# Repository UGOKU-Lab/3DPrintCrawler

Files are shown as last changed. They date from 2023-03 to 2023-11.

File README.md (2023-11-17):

# 3DPrintCrawlerについて
タミヤのラダーチェーンとギアボックス、3Dプリントパーツのみで製作したクローラユニットです。  
使用するネジ類もタミヤのセットの付属品のみで完結します。  
ラダーチェーンに履板をパッチっとはめる方式なので履板形状を自由に設計できます。

本リポジトリはみなさんにより早くデータを提供するため、README含め不完全な状態で公開する、β版的な位置づけである点をご了承ください。
ご意見や改善案のある方は、Twitter、Issues、プルリクなどで問い合わせ及び提案お願いします。
次期Versionの開発に生かします。

 

# 製作に必要なタミヤの部品
1ユニット製作するのに、それぞれ1セットずつ必要になります。

- 楽しい工作シリーズ（パーツ）No.142 ラダーチェーン＆スプロケットセット  
https://www.tamiya.com/japan/products/70142/index.html

- テクニクラフトシリーズ No.7　4速パワーギヤボックスHE  
https://www.tamiya.com/japan/products/72007/index.html

# データの説明
- フォルダ「stl」：すぐにプリントしたい方向けに各パーツをstlで置いてあります。
- フォルダ「step」：組み立ての確認用、データ編集用です。左右接続したアセンブリのデータと履板のデータをstepで置いてあります。

## データ留意事項
- 履板をプリントする際はアセンブリファイル内のものではなく、個別のデータをご使用ください。プリント用に調整してあります。きつすぎたり、ゆるすぎたりする場合はstepから編集してください。
- アセンブリファイルに含まれる基板はMultiBoardMiniという作者が開発している汎用基板です。こちらについてはデータ公開準備中です。

# 3Dプリント
プリントには250x250サイズ程度の3Dプリンタが必要になります。より普及している220x220サイズのプリンタではプリントできないのでご注意ください。（後日220x220サイズのプリンタでもプリント可能な全長短縮版もアップ予定ですのでもう少々お待ちください。）
すべての部品において充填率は15%ほどで問題ないと思います。
## main-flame
250x250サイズのプリンタでも収めるためには斜めに配置する必要があります。
手前の工具穴、左右接続パーツ挿入部、長穴にはサポートが不要なためサポートブロッカーを配置します。
左右接続パーツ挿入部は条件によりフィラメントが垂れ下がることがありますが、その場合はやすり等で除去してください。おそらくサポート材を外すより楽です。



## track-shoe
サポート材は不要ですが、接地面積が小さいため外れやすいです。外れる場合はBrimを使いましょう。外れるリスクをとるか、Brimを除去する手間をとるかといったかんじです。



## その他パーツ
その他のパーツは積層方向が正しければ特段留意点はありません。

# 組み立て
## 使用工具
- ＋ドライバーNo.2・2本（1本は細軸が望ましい）
- ナットドライバ 5.5
- ニッパー

## 組み立て参考図
- スプロケットとクランクプレートの固定：3×8mmタッピングビス（ラダーチェーン付属）　　
- ギアボックス固定：3×10mmタッピングビス（ギヤボックス付属）
- アイドラシャフト固定：3×12mmタッピングビス（ラダーチェーン付属）















# ライセンス
<br />この 作品 は <a rel="license" href="http://creativecommons.org/licenses/by-sa/4.0/deed.ja">クリエイティブ・コモンズ 表示 4.0 国際 ライセンス</a>の下に提供されています。

本データおよび本データにより製作したクローラーは良識の範囲で自由に非営利、営利問わず使用できます。また、改変、再配布も可能です。
ただし、再配布の際には「3DPrintCrawler」と本リポジトリのリンクを掲載してください。  
また、本データにより製作したクローラーを公の場で使用、SNS等で紹介する場合はなるべく「#3DPrintCrawler」と本リポジトリのリンクを掲載してください。  
また、本データにより生じた損害等の一切の責任を負いかねますので、ご了承ください。

# 今後の展望
今回はInventor（学生ライセンス）でデータを作成[^1]しましたが、次期バージョンはFreeCADなどフリーかつオープンソースの3DCADでデータを作成し、だれでもネイティブで編集できるようにしようと考えています。
また、将来的には寸法を入力するとそのサイズの3Dプリントクローラの3Dモデルが自動生成されるツールにまで発展させたいと考えています。
[^1]:データは学生時代に製作したものです。
# 最後に
本作品は作者の元インターン先でもある**株式会社CuboRex**のクローラユニット「**CuGo**」シリーズにもインスピレーションを受けています。  
また、株式会社タミヤの製品があってこそ実現できました。  
さらに、3Dプリント履板をタミヤのラダーチェーンにはめるというアイデアは研究室にあった機体より得たものです。  
この場をお借りして株式会社CuboRex、株式会社タミヤ、そして先述の機体を製作した研究室の先輩に敬意を表します。

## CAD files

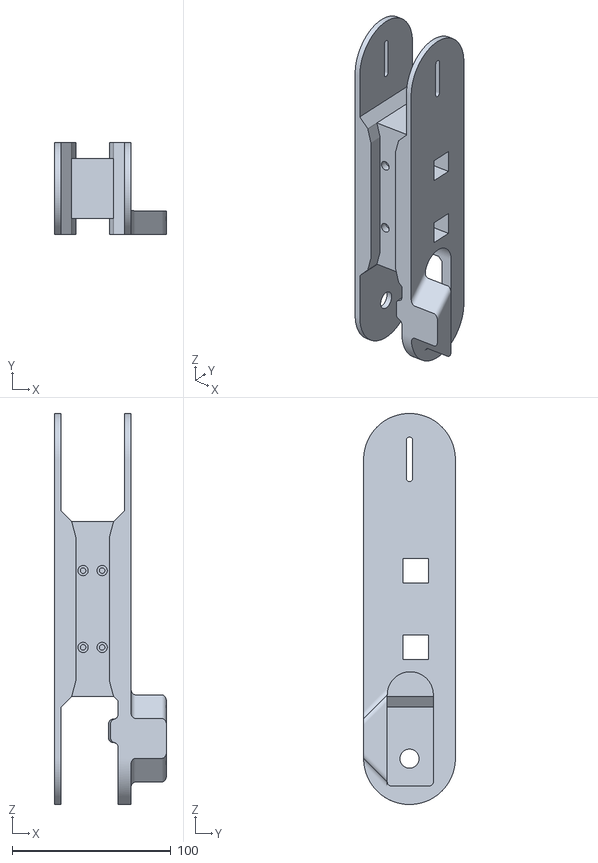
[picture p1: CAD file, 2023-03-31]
stl/main-flame_R.stl
70.5 x 57.7 x 246.0

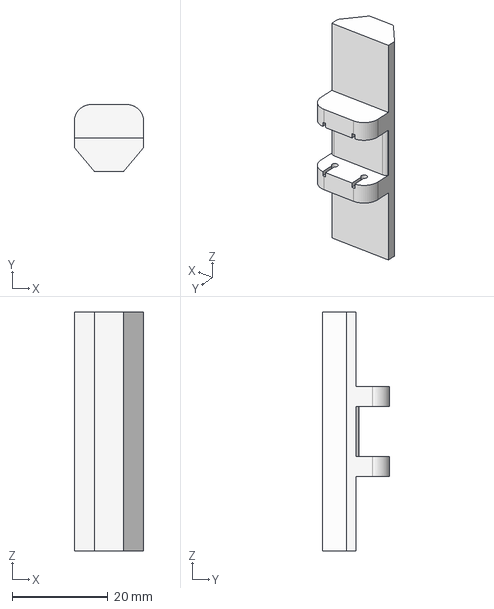
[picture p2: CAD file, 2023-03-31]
step/track-shoe_for_0.5mm-nozzle.step
14.5 x 14.0 x 50.0 mm

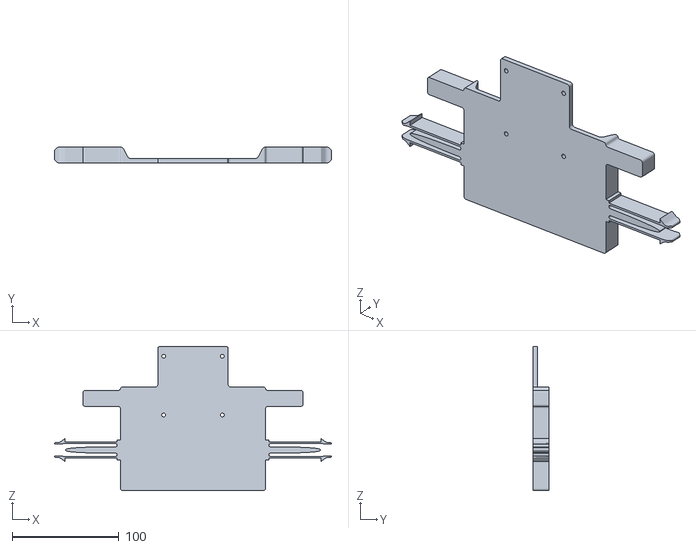
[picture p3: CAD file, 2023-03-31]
stl/center-flame.stl
259.4 x 15.0 x 135.0

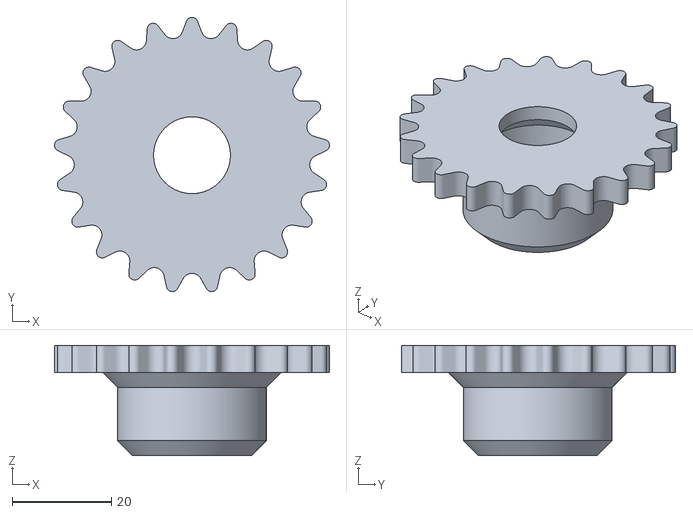
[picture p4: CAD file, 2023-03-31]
stl/Idler.stl
55.5 x 55.4 x 22.2

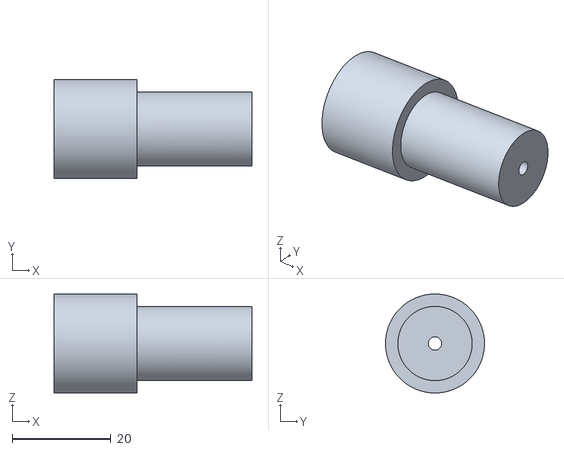
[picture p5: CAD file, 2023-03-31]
stl/idler_shaft.stl
40.0 x 20.0 x 20.0

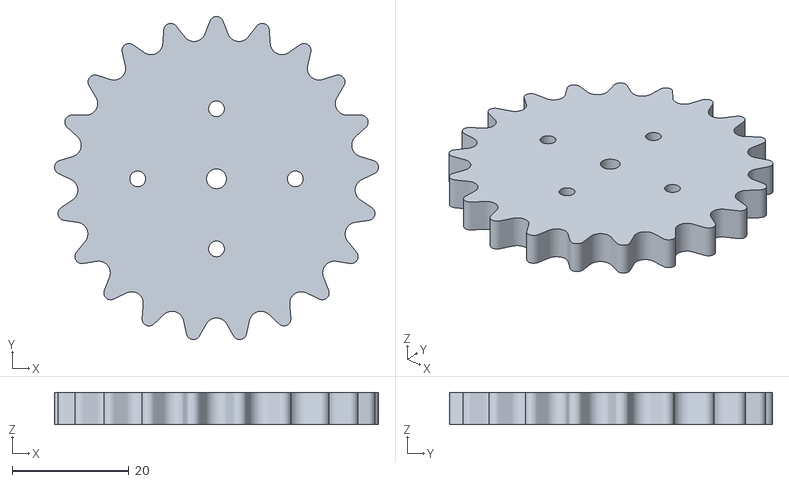
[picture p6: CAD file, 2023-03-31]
stl/sproket.stl
55.5 x 55.4 x 5.50

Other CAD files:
stl/main-flame_L.stl
step/track-shoe_for_0.4mm-nozzle.step
stl/track-shoe_0.5mm_nozzle.stl
stl/track-shoe_0.4mm_nozzle.stl

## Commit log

2023-03-31 add stl
    [Idler.stl, idler_shaft.stl, main-flame_L.stl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]
2023-03-31 add center-flame stl
    [center-flame.stl]
2023-03-31 add step
    [track-shoe_for_0.4mm-nozzle.step, track-shoe_for_0.5mm-nozzle.step]
2023-09-23 Update README.md
    MultiBoardMiniのデータの公開について諸事情により準備中に変更

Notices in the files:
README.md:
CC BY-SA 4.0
